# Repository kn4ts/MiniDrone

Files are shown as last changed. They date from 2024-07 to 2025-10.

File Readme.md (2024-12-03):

# Mini Drone
100g以下程度の小型ドローン製作を目指すプロジェクトです  

# 目次
1. [概要](#概要)
2. [マイコンのプログラムの基本構成](#マイコンのプログラムの基本構成)
3. [モータ駆動回路の基本構成](#モータ駆動回路の基本構成)
    - [モータの回転方向とプロペラについて](#モータの回転方向とプロペラについて)
    - [PWM出力・推力・電流の予備実験結果](#推力と電流とPWM値の測定実験)
4. [機体の作成](#機体の作成)
    - [概要](#部品の概要)
    - [機体の設計](#機体の設計)
    - [電気回路の構成](#電気回路の構成)
5. [ドローン制御系の基本構成](#ドローン制御系の基本構成)
6. [トラブルシュート](#トラブルシュート)
7. [参考ページ](#references)

# 概要
無線通信が可能なマイコンをフライトコントローラとして用い，地上局（PC）からのおおまかな指令をもとに飛行する小型ドローンを製作します．
特に制御実験に使用することを目指して，以下の要件を設定します．
+ 設定した制御周期を維持できること
+ 内界センサの計測値や計算した制御入力を逐次的に外部に出力できること
+ オリジナルの制御則やフィルタなどを容易に試せること

これらを実現するために，次のようなコードの流れを考えます．
（ここではマイコンとして`Arduino nano 33 BLE`（[https://ssci.to/7667](https://ssci.to/7667)）を使用することを想定していますが，相当の機能を持つマイコンであれば同様に構成可能と思います）

```mermaid
sequenceDiagram # シーケンス図の定義
    autonumber # 信号に番号をつける

    # 各要素の定義
    participant DebugDO as DO2<br>(デジタル出力ポート) # デバッグ用DOポート
    participant Sen as 測距センサ<br>(VL53L0X) # I2C接続
    participant Micon as マイコン
    participant PC as 地上局PC  # PC（地上局）

    Micon ->> Sen : I2C接続，周期設定
    PC ->> Micon: BLE接続

    loop BLE接続の持続 # ループの定義

        alt 制御用タイマーのフラグがオン # if文
            Note over Micon : IMU計測値から姿勢更新・取得
            Note over Micon : 現在の高度を取得
            # rect rgba(255, 0, 255, 0.2) # 色付け
            Note over Micon : 制御則の計算
            # end
            Note over Micon : PWM出力値更新 => FETへ

            Micon -->> DebugDO : DOポートをトグル（デバッグ用）
            Note over DebugDO : オシロスコープで100Hz出ているか確認
        end

        alt BLE通信用タイマーのフラグがオン
            Note over Micon : 現在の各内部変数からメッセージ作成
            # rect rgba(255, 0, 255, 0.2) # 色付け
            Micon ->> PC : BLE通信，メッセージ送信
            opt データロガー継続
                Note over PC : ファイルへ書き出し
            end
            # end
            Micon -->> PC : シリアル通信（デバッグ用）
        end

        alt 測距センサ用タイマーのフラグがオン
            Micon ->>+ Sen : I2C通信，測定値を要求
            Note over Sen : 注意：未準備だとブロック
            Sen ->>- Micon : I2C通信，測定値を返す
        end

        opt BLE通信による指令送信
            PC ->> Micon : BLE通信，指令送信
            Note over Micon : 指令解釈・モード変更
        end
    end

```
前述のタスクを達成しつつ制御周期を一定に維持するために，3つのタイマーを用いる構成としています．  

まず1つ目は制御則の動作周期をはかるタイマー`tmCon`で，ドローン制御で必要とされている100Hzに設定しています．こちらはデジタル出力ピンにパルス出力をさせてオシロスコープで100Hzが実現できることを確認しました．

2つ目はBLE通信（地上局への送信）のタイミングをはかるタイマー`tmBLE`で，これは`Arduino nano 33 BLE`マイコンで試したところ10Hz程度が安定する最高の速度でしたので10Hz程度で使用しています．（もちろん理想は制御周期と同じ100Hzでの通信ですが...）  

3つ目は機体高度を計測する測距センサから値を読みだす周期をはかるタイマー`tmToF`です．
使用するセンサ（VL53L0Xユニット，I2C接続）の仕様上，計測値の精度を高めるために数十ms必要で，また計測値が準備できていないと読み出し指令がブロックされる（※）とのことなので，少し長めに約33Hz(=30ms)の周期で読み込む時間管理をしています．
（こちらも制御周期と同じ100Hzで読むことが理想なのですが）

※【将来の課題】VL53L0XのGPIO1ピンはセンサが新しいデータを準備したときにトリガーされるそうなので，このピンをデジタルピンで監視しておけば回避できそうです．

またマイコンへの地上局からの指令もBLE通信を使用することにしていますが，こちらは頻繁な通信をしないという前提で，とりあえず時間管理なしで運用しています．今後，地上局も含めた閉ループを高速周期で構成する必要がでてくれば，そのためのタイマーを実装する必要がありそうです．

## 使用するライブラリ
+ `ArduinoBLE.h` ... BLE(Bluetooth Low Energy)を使用するためのライブラリ．
+ `Arduino_LSM9DS1.h` ... 9軸IMUのライブラリ．
+ `VL53L0X.h` ... ToF(Time of Flight)測距センサのライブラリ．

## 環境構築
1. Arduino IDE をインストール
2. Arduino IDE のボードマネージャから上記ライブラリをインストール  
参考：https://qiita.com/konikoni428/items/f4c7154ccf1eafd331c9

上記に加えて，BLE通信の動作確認のためにターミナルが使えると便利です．たとえばアプリの`LightBlue`など．

# マイコンのプログラムの基本構成
フライトコントローラの機能ごとにソースコードを分けて，メイン（`miniDrone.ino`）から呼び出して使用する構造にします．
これにより，機能の追加実装やテスト，複数人での開発が容易になることが期待できます．
```mermaid
graph TD
    classDef h fill:transparent, stroke:#9370DB
    classDef cpp fill:transparent
    classDef ino fill:transparent

    %% style some-group fill:transparent,stroke:#9370DB
    subgraph BLE [BLE機能のユニット]
        subgraph hBT [BLE.h]
            conBT[定数の定義]
            ~~~ proBT[関数のプロトタイプ宣言]
        end
        subgraph cppBT [BLE.cpp]
            valBT[変数の定義]
            ~~~ funBT[関数の中身の実装]
        end
        hBT --インクルード--> cppBT
        %%funBT --予め定義--> proBT
    end
    subgraph ControlTimer [Timer機能のユニット]
        subgraph hCT [ControlTimer.h]
            conCT[定数の定義]
            ~~~ proCT[関数のプロトタイプ宣言]
        end
        subgraph cppCT [ControlTimer.cpp]
            valCT[変数の定義]
            ~~~ funCT[関数の中身の実装]
        end
        hCT --インクルード--> cppCT
    end
    subgraph UnitX [・・・機能のユニット]
        subgraph hX [xxx.h]
            conX[定数の定義]
            ~~~ proX[関数のプロトタイプ宣言]
        end
        subgraph cppX [xxx.cpp]
            valX[変数の定義]
            ~~~ funX[関数の中身の実装]
        end
        hX --インクルード--> cppX
    end
    subgraph miniDrone[miniDrone.ino]
        inc1["#include "必要な機能1""]
        inc2["#include "必要な機能2""]
        incx["#include "必要な機能xxx""]

        subgraph Global[グローバル変数・関数]
            global[グローバル変数の定義]
            ~~~ globalfun[関数の定義]
        end

        subgraph loop[loop関数]
            callfunX[関数の使用]
        end
        
        setup[setup関数]

        inc1 -.- inc2
        inc2 -.- incx
        incx -.-> setup

        setup --> loop
        %%loop --ループ--> loop

        Global --> loop
        funX -.-関数の呼び出し-.-> callfunX
        %%funX -.-関数の呼び出し-.-> setup

        hBT --インクルード--> inc1
        hCT --インクルード--> inc2
        hX --インクルード--> incx
    end
```

最終的にはオリジナルの制御則やフィルタのコードは`Control.cpp`と`Control.h`のようなファイルにまとめるようにして，同じようにメインコードから呼び出して使用するような運用を考えています．
これにより設計者が極力メインコードを触ることなく制御則やフィルタを試せるようにしたいです．

# モータ駆動回路の基本構成
今回は設計を簡単にするために駆動系としてブラシ付きDCモータを使用することにします．
基本となるモータ1つ分の駆動回路を以下に示します．
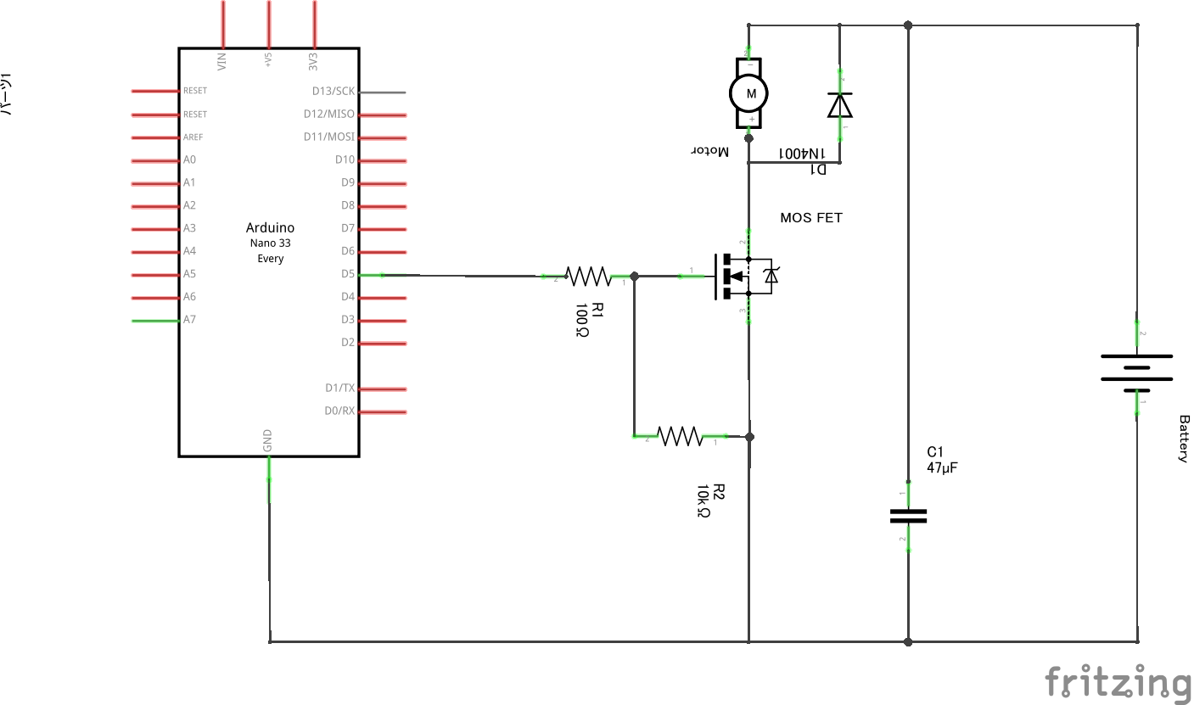
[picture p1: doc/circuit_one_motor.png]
回路図


ここではバッテリーからモータの駆動電流をとることとし，N-ch MOS FETを使って，駆動回路に流れる電流をマイコンのデジタル出力ピンから間接的に操作します．

また図では省略していますが，マイコンの電源はUSBケーブルから供給することを想定しています．
電源が異なるのでグラウンド（`GND`）の共通化を忘れないように注意してください．

この回路に使用している参考部品は以下の通りです．

**表1. モータ駆動回路の構成部品**
| 記号 | 名称 | 用途 | 型番  | 主な選定理由 |
| ----- | --- | -----| --- | ---|
| Motor | ブラシ付きDCモータ  | ロータ  | [8520モータ](https://www.amazon.co.jp/s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) | 100gクラスのドローン`Tello`の予備部品が流通しているため |
| MOS FET | N-ch 電界効果トランジスタ | 駆動回路のスイッチング | [2SK4017](https://www.google.com/search?client=firefox-b-d&q=2SK4017)など．部品のピン配置は[こちら](https://akizukidenshi.com/goodsaffix/2SK4017.pdf)を参照のこと． | 連続2A以上流せて，オン抵抗が低いFETを選定  |
| D1 | ダイオード | フライバックダイオード（逆起電力対策） | [SB240LES](https://akizukidenshi.com/catalog/g/g116419/)など | 駆動電圧より十分高い耐圧で，かつ連続2A以上流せるものを選定 |
| C1 | キャパシタ | バイパスコンデンサ（パスコン）| [積層セラミックコンデンサー 47μF16V](https://akizukidenshi.com/catalog/g/g104917/)など | 数十μFの容量があること |
| R1 | 抵抗器 | 電流調整用 | [1/4Wカーボン抵抗100Ω](https://www.marutsu.co.jp/pc/i/107016/)など | - |
| R2 | 抵抗器 | プルダウン抵抗？  | [1/4Wカーボン抵抗10kΩ](https://www.marutsu.co.jp/pc/i/107028/)など | - |
| Battery | 1S LiPoバッテリー  | モータの駆動電源  | [BETAFPV BT2.0 300mAh 1S 30Cバッテリー](https://amzn.asia/d/6Hk7pkt)など | 軽量かつ取扱いが容易で，連続8A以上の放電能力があること |

なお，こちらの回路を使用してモータを駆動させるテストコードは[こちら](https://github.com/kn4ts/MiniDrone/releases/tag/actuator-test)からアクセスできます．
使い方は，BLE通信で接続後，String型で"1"~"9"を送信すると`20`～`255`までのPWM値をD5～D8ピンから出力します（"0"を送ると停止）．モータが回転するので注意してください．

## モータの回転方向とプロペラについて
なおプロペラは`Tello`のスペアパーツとして流通している[こちら](https://amzn.asia/d/75Xps07)やその代替品を使用します．
8520モータの軸に差し込むだけで使用可能です．  
なお8520モータには2種類あり，線の色で見分けられるようです．
線の色と回転方向は以下の表の通りです．

**表2. モータの回転方向**
|モータの線の色|回転方向|
| --- | --- |
|白(-側)と黒(+側)|CW（時計まわり）|
|青(-側)と黒(+側)|CCW（反時計回り）|

そしてこのモータの回転方向に合ったプロペラを取り付けます．
また4つのロータで飛行するクワッドロータドローンでは，対角に同じ回転方向のロータを配置する必要がありますので注意してください．

## 推力と電流とPWM値の測定実験
前述の回路構成をもとに4つのロータを駆動する予備的な実験を行いました．
実験の様子を以下に示します．
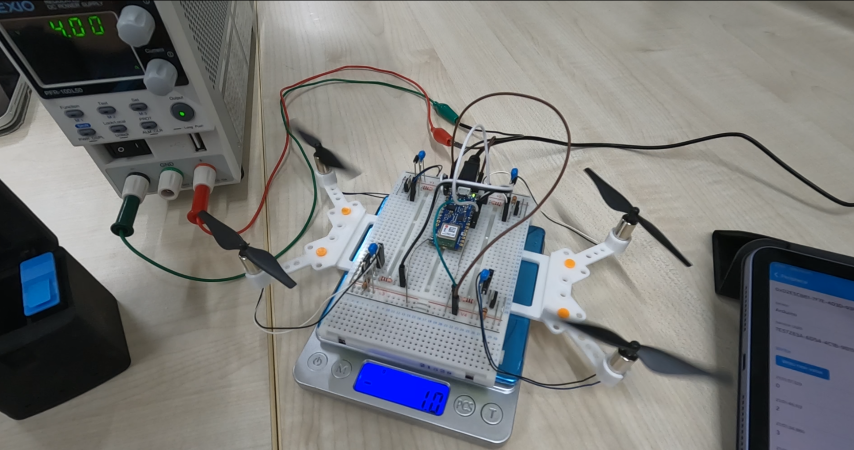
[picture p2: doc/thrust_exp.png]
予備実験の装置構成


ここではモータ駆動用の電源として安定化電源を使用（4.00Vで最大電流値10Aに設定）し，マイコン電源はUSBから供給しました．
またマイコン含む回路部分全体を重量計の上に置き，いくつかのPWM値で4つのロータを同時に駆動した際の重量計の値の減少量とそのときの電源装置の出力電流をメモしました．

その結果を1つの図にプロットしたものを以下に示します．
なお，これらの計測値は定常状態のもの（目視で値が落ち着いたところで読み取ったもの）であるため，結果は参考値です．

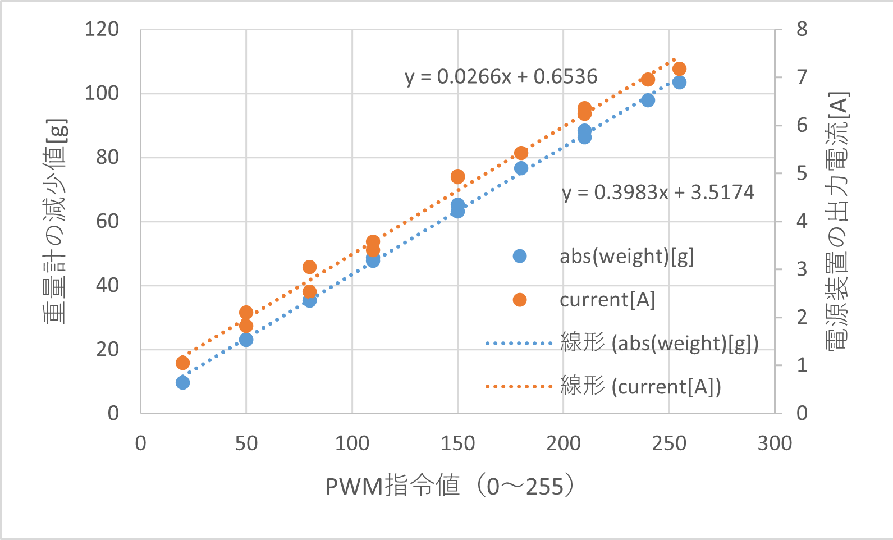
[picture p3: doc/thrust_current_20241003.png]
推力-電流-PWM指令値の測定結果


この結果から，マイコンに指令するPWM値に対して推力（正確には重量計表示の減少量[g]），電流[A]がいずれもほぼ線形に推移していることが読み取れます．

また推力と電流値を比較することで，機体重量に対する使用バッテリーに要求される放電能力や，飛行可能時間を概算できます．

# 機体の作成
## 部品の概要
+ Arduino nano 33 BLE ... BLEモジュールとIMUが搭載されたマイコン（[https://ssci.to/7667](https://ssci.to/7667)）
+ VL53L0X Time-of-Flight 距離センサモジュール ... ToF測距センサ（[https://ssci.to/2894](https://ssci.to/2894)）
+ 電圧レギュレータ ... マイコン電源用．5V出力ステップアップ／ステップダウン電圧レギュレータ（[https://ssci.to/1168](https://ssci.to/1168)）

## 機体の設計
機体のフレームは[電気回路の設計・配置](#電気回路の構成)と合わせて，サイズや構造を考えて設計します．
具体的には，モータや基板の固定方法やセンサの配置，バッテリーの搭載位置などを検討する必要があります．
また機体の中心からみて重量の偏りがない方が，制御設計や飛行特性が扱いやすいものになりそうです．

[（参考）機体フレームのSTLデータ](./hardware/Frame/frame_A_ver3.stl)  
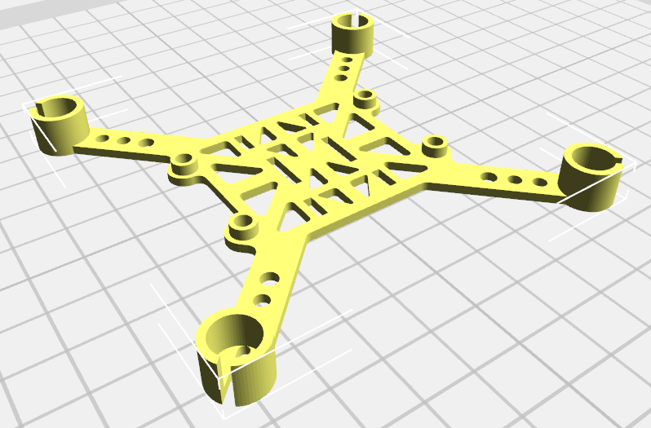
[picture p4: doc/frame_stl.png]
機体フレームの設計


## 電気回路の構成
以下に駆動系・測距センサ・電圧レギュレータを含めた全体の回路図を示します．

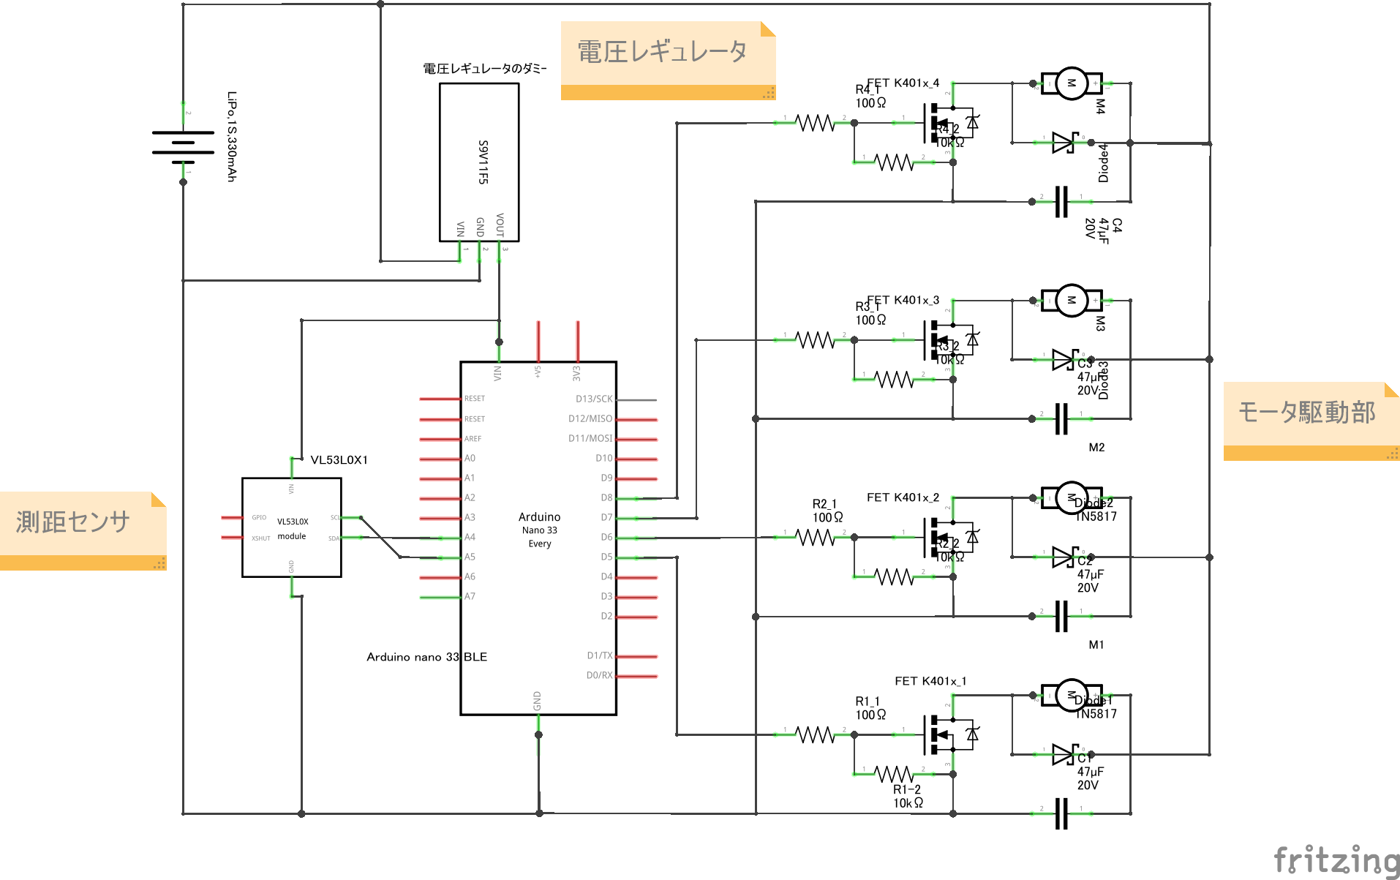
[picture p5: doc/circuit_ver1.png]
ドローン全体の回路図


ドローンではマイコン電源もバッテリーからとる必要があるので，電圧レギュレータを挟んで昇降圧したラインをマイコンの`VIN`ピンに接続しています．
また測距センサの駆動電源も，同じくレギュレータからとるようにしています．

こちらの回路図をもとに実体配線図を作成し，基板上に部品を配置してください．
回路や実体配線図の製作については，[fritzing](https://fritzing.org/)や[PasS](http://uaubn.g2.xrea.com/pass/)，Eagleなどを使用すると便利です．

[（参考）回路図データ](./circuit/fritzing/circuit_ver1.fzz)  
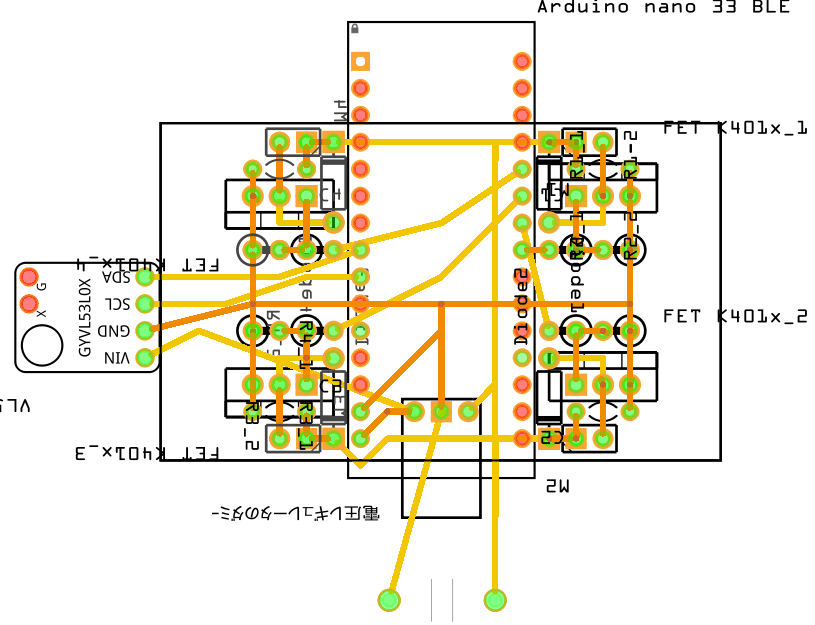
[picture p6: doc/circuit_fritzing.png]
実体配線図の一例


# ドローン制御系の基本構成
ドローンの姿勢（ロール，ピッチ．ヨー）角と高度を制御するための制御系のブロック線図の概要を以下に示します．

ブロック線図

ここでは，制御対象（プラント）への入力信号（制御入力）を各ロータの駆動回路（[こちらです](#モータ駆動回路の基本構成)）をスイッチングするPWM信号値（デューティ比）とし，出力信号（制御量）を機体の姿勢角および高度として解釈します．

以下では，このドローンの制御系を構成するために必要な3つの要素についてそれぞれ説明します．

## ①姿勢・高度推定器
制御量である姿勢角と高度はそれぞれ9軸IMUと測距センサにより計測します．
ただしこれらの計測値はノイズやバイアス成分を含んでいると考えられるため，計測された信号をもとに姿勢や高度の推定器を構成します．
この推定器としては，例えば相補フィルタやカルマンフィルタが使用されることが多いようです．

## ②制御器
そして（推定器で求められた）姿勢角と高度に対してそれぞれ制御器を構成します．
制御器は制御量と参照値（目標値）をもとに，次にどのような制御入力を制御対象に加えるかを決定する機構です．

ここでは姿勢角制御器は機体の3つの回転軸（ロール，ピッチ，ヨー）まわりに要求されるトルクに相当する信号値を計算し，高度制御器は4つのロータに要求される総推力に相当する信号値を計算する，と解釈しています．
上の図では，これらの3つのトルクと1つの総推力をまとめて要求制御力と表現しています．
要求制御力をベクトルで表現するとトルク3つと総推力1つで合計4次元を持ちます．

## ③分配器（ミキシング則）
要求制御力はそのままでは制御入力として使用できないため，要求制御力をもとに各ロータを駆動するPWM値を計算する機構が必要で，これを上図では分配器（ミキシング則）と表現しています．
分配器を設計する上では，姿勢角の軸のとり方とプロペラの配置・回転方向を考慮する必要があります．

以上の推定器・制御器・分配器を適切に設計してドローンの制御系を構成します．
なお，これら3つをまとめて制御器と呼ぶ場合もあります．

# ドローン制御則の実装
`miniDrone.ino`の制御周期のタイミングにおける具体的な計算の流れを以下のシーケンス図で説明します．

```mermaid
sequenceDiagram # シーケンス図の定義
    autonumber # 信号に番号をつける

    # 各要素の定義
    participant Main as 制御周期における処理 <br>（miniDrone.inoの中）
    participant Class as 

    opt IMU計測値の更新・取得
        Note right of Class: IntegratedIMU.cpp
        Main ->> Class : updateIMUAttitudeVal() <br> （姿勢値の更新指令）
        Class ->> Main : ATTITUDE = getIMUAttitude_wo_b() <br> （バイアス値抜きの姿勢を取得）
        Class ->> Main : ANG_VEL = getIMUAngularVelocity_wo_b() <br> （バイアス値抜きの姿勢角速度を取得）
        Class ->> Main : MAG = getIMUMag() <br> （地磁気センサの値を取得） 
    end

    opt 高度計測値の取得
        Note right of Class: SencorI2C.cpp
        Class ->> Main : ALTITUDE = getAltitudeVal_wo_b() <br> （バイアス値抜きの高度を取得）
    end

    opt 姿勢・高度制御則の計算例
        Note right of Class: Control.cpp <br> （構成例）
        Main ->> Class : set{Roll,Pitch}Reference( REF ) <br> （姿勢角の参照値をセット）
        opt 制御器の計算 
        Main -> Class : PWMs = controller_demo( ATTITUDE, ALTITUDE ) <br> （フィードバック信号である姿勢，高度を引数として渡す）
            Note over Class : フィルタ計算
            Note over Class : 制御則計算
            Note over Class : 分配器計算
        Class ->> Main : PWMs = controller_demo( ATTITUDE, ALTITUDE ) <br> （計算結果のPWM信号値の配列の先頭ポインタを返す）
        end
    end

    alt Arm状態なら
        Note right of Class: Actuator.cpp
        Main ->> Class : REAL_PWMs = driveActuator( PWMs ) <br> （PWM指令値を使ってロータを駆動，<br> 飽和後のPWMsを返す）
    else Disarm状態なら
        Main ->> Class : REAL_PWMs = driveActuator( PWM_ZEROs ) <br> （0の入力を使ってロータを駆動（つまり停止），<br> 飽和後のPWMsを返す）
    end

```
---
---

# トラブルシュート
## デバイスマネージャで COM xx が認識されない
下記を試す．  
+ PCの再起動
+ Arduino IDE のバージョン更新確認
+ Arduino IDE でボード情報の更新
+ マイコンのリセットボタンを押しながら接続

コードが間違っていてマイコン側のUSB Serialが機能しなくなっている可能性がある．その場合は以下を試す．
+ マイコンのリセットボタンをダブルタップ -> 違うCOMポートとして認識 -> 認識したCOMポートで正しいコードを書き込み

## References
### フォルダ構成は下記を参考にした  
+ https://qiita.com/somehiro/items/6a6d954be159b6a5fccd  
+ https://zenn.dev/skou/articles/7a49ca2f9f0fcc

### 駆動系の電気回路は下記を参考にした
+ https://www.remma.net/?p=1341

### COMが認識されなくなる問題のトラブルシュート  
+ https://detail.chiebukuro.yahoo.co.jp/qa/question_detail/q11263532971

### Mermaidの参考ページ
+ https://qiita.com/run1000dori/items/90f91687cfe7ece50020

### VSCodeでDrawioを使って作図する拡張機能について
+ https://otepipi.hatenablog.com/entry/2020/05/25/192844

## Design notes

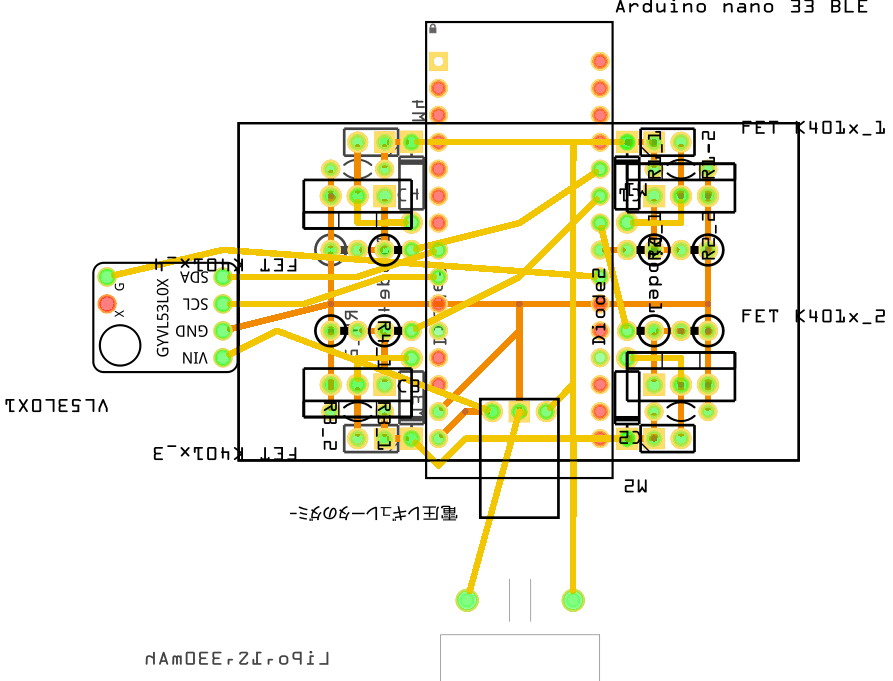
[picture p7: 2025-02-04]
doc/circuit_ver2_fritzing.png

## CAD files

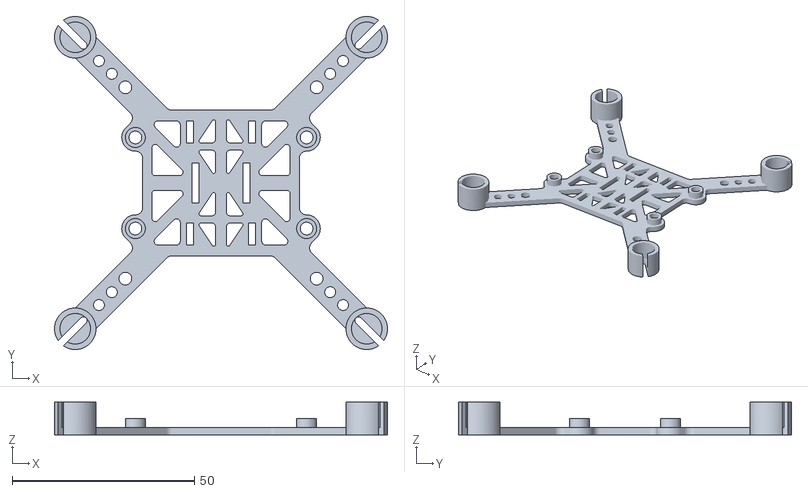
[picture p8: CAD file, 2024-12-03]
hardware/Frame/frame_A_ver3.1.stl
91.4 x 91.4 x 9.00

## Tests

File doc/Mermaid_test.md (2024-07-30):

# Mermaid をMarkdownで使うテスト
```mermaid
block-beta

%% 信号用に枠線なしのブロックをクラスとして定義
classDef signal stroke-width:0px
%% 信号分岐用に黒塗りのブロックをクラスとして定義
classDef split fill:black

columns 9
ref["参照入力"] plus(("+")) space cont["制御器"] space plant["プラント"] split1((" ")) space out["出力"]
space:9
space lb["└"] space:4 rb["┘"]

class ref,out,lb,rb signal
class split1 split

ref --> plus
plus --> cont
cont --> plant
plant --> split1
lb --> plus
split1 --> rb
split1 --> out
rb --> lb

```
TEST

```mermaid
flowchart LR
    Reference --> plus1(("+"))
    plus1 --- Controller
    Controller --- Plant
    Plant --- split1((" "))
    split1 --> Output

    %%Output --- Minus1["-1"]

    split1 --- Minus1
    Minus1 --> plus1
    %%<!-- Null2 --> plus1 -->

    classDef signal stroke:none
    classDef split fill:black,stroke:white
    classDef plusminus stroke:white

    class Reference,Output signal
    class split1 split
    class plus1 plusminus
```

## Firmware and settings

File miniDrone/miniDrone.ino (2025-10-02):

/* ==================================================================
  メインのソースコード
================================================================== */
#include "src/inc/miniDrone.h" // 全体のヘッダファイル


/* ==================================================================
  セットアップ関数
================================================================== */
void setup() {
  /* 出力ピンの設定 */
  pinMode( LED_BUILTIN, OUTPUT ); // 内臓LEDの設定（デバッグ用）
  pinMode( STATE_DO, OUTPUT );  // 制御周期確認用DOポートの設定（デバッグ用）
  setupPWMpin(); // PWM出力ピンの初期化

  /* シリアル通信の初期設定 */
  openSerial();

  /* BLEの初期設定 */
  if( !setupBLE() ){
    // 失敗したらエラー表示で止まる
    while(1){
      Serial.println("BLE setup error!");
      delay(2000);
    };
  }

  /* タイマーの初期設定 */
  setupTimer();

  /* 内臓IMUの初期化 */
  if( !initIMU() ){
    // 失敗したらエラー表示で止まる
    while(1){
      Serial.println("IMU setup error!");
      digitalWrite( LED_BUILTIN, HIGH );
      delay(500);
      digitalWrite( LED_BUILTIN, LOW );
      delay(500);
    };
  }

  /* I2Cセンサの初期化 */
  if( !initSensorI2C() ){
    // 失敗したらエラー表示
    Serial.println("I2C sensor setup error!");
    delay(2000);
  }

}

/* ==================================================================
  メインループ関数
================================================================== */
void loop() {
  /* BLE接続を試行する */
  listenBLE(); // セントラル機器との接続確認
  pollBLE(); // BLEスタックの更新

  /* BLE接続されていたら実行される部分 */
  if ( isConnectedToPeripheral() ){ // セントラルがペリフェラルに接続されているかの確認
    /* BLEセントラルに接続されている間ループ */
    while ( centralStillConnected() ){

      // BLE通信の指令の受信・解釈
      mode = modeDetectionBLE();

      // モードに応じた動作（一度きり実行）
      switch (mode){
        // 制御開始準備
        case MODE_CONTROL_STANDBY:  // mode が CONTROL_STANDBY なら
          setAltitudeReference(300); mode = MODE_CONTROL; break; // 高度目標値をセット・モードをCONTROLへ移行
        
        // センサキャリブレーション
        case MODE_CALIBRATE_SENSORS: // センサキャリブレーション
          calibrateSensors();
          //calibrateGyroBias(); // ジャイロセンサのバイアスを再取得
          mode = MODE_NORMAL; break;

        // 姿勢角キャリブレーション
        case MODE_CALIBRATE_ATTITUDE: // 姿勢角キャリブレーション
          calibrateAttitude();
          mode = MODE_NORMAL; break;

        // Arm
        case MODE_ARM:
          armDrone();
          //arm = true;
          initializeController(); // 制御器をリセット
          mode = MODE_NORMAL; break;

        /* 目標値セット */
        //case MODE_FORWARD:
        //  cnt_pit = -cnt_MAX; mode = MODE_NORMAL; break; // カウンタを-最大値へ
        //case MODE_BACKWARD:
        //  cnt_pit =  cnt_MAX; mode = MODE_NORMAL; break; // カウンタを最大値へ
        //case MODE_LEFT:
        //  cnt_rol = -cnt_MAX; mode = MODE_NORMAL; break; // カウンタを最大値へ
        //case MODE_RIGHT:
        //  cnt_rol =  cnt_MAX; mode = MODE_NORMAL; break; // カウンタを最大値へ

        /* 停止モード */
        case MODE_STOP: 
          disarmDrone();
          break;

        /* 上記以外の場合はスルー */
        default:
          //initializeController(); // 制御器をリセット
          //uc_pointer = setUc( 0, 0, 0, 0 ); // 制御器出力をすべて0に
          break;
      }


      /* -------------------------------
         制御周期タイマー処理のはじまり
      ------------------------------- */
      if ( getTmConFlag() ){
        setTmConFlag(false); // タイマー割込みフラグをおろす

        /*
          指令値カウンタの確認・処理
        */ 
        updateRollPitchReference( cnt_rol, cnt_pit ); // ロール・ピッチ角指令値の更新

        // IMUセンサ値を用いた姿勢角の更新
        //updateIMUAttitudeVal();
        updateIMUAttitudeVal_ver2();

        // IMUで計算した値を取得
        att = getIMUAttitude_wo_b(); // 姿勢を取得
        anv = getIMUAngularVelocity_wo_b(); // 角速度を取得
        // 地磁気計測値を取得
        // mag = getIMUMag(); 

        /* ToFセンサから届いている最新の高度を取得 */
        if ( getToFFlag() ){
          setToFFlag(false); // ToFセンサフラグをおろす
          // 注意：測定値が準備できていないとブロックする
          //updateAltitudeVal();
          updateAltitudeVal();
          alt = getFilteredAltitudeVal_wo_b();
        }

        /*
          高度・姿勢の異常検知
        */
        if( abs(att[0]) > 90 ){ mode = MODE_STOP; }; // ロール角が異常ならモードを0に
        if( abs(att[1]) > 90 ){ mode = MODE_STOP; }; // ピッチ角が異常ならモードを0に

        /*
          モードに応じた動作（継続実行）
          モードの一つとして制御則を実装する
        */
        switch (mode){
          /* 停止モード */
          case MODE_STOP: // mode が 0 ならロータ停止
            disarmDrone();  // ドローンをディスアーム
            uc_pointer = setUc( 0, 0, 0, 0 ); break;

          /* 全モータの動作テストモード */
          case MODE_TEST_ALL_MOTORS:
            uc_pointer = setUc( 20, 20, 20, 20 ); break; // 全モータをPWM値20で回す指令
          
          /* 制御モード */
          case MODE_CONTROL: // mode が 10 なら制御実行
            // 制御モード時の異常検知
            if( alt > 2000 ){ mode = MODE_STOP; };       // 高度計測値が異常ならモードを0に

            // 制御則の計算
            uc_pointer = controller_demo( att, alt ); // 制御則関数
            uc[0] = uc_pointer[0]; // 制御器出力をucにセット
            uc[1] = uc_pointer[1];
            uc[2] = uc_pointer[2];
            uc[3] = uc_pointer[3];
            break;
          
          /* ジンバル制御モード（ロール・ピッチ） */
          case MODE_GIMBAL_ROLL_PITCH: // 2DoFジンバル（ロールピッチ軸）の姿勢制御モード
            //uc_pointer = gimbalControl_demo( att, alt ); // ジンバル使用時の制御則
            uc_pointer = gimbalControl_demo( att, anv, alt ); // ジンバル使用時の制御則
            uc[0] = uc_pointer[0]; // 制御器出力をucにセット
            uc[1] = uc_pointer[1];
            uc[2] = uc_pointer[2];
            uc[3] = uc_pointer[3];
            break;
          
          /* ジンバル制御モード（ロールのみ） */
          case MODE_GIMBAL_ROLL: // 1DoFジンバル（ロール軸のみ）の姿勢制御モード
            //uc_pointer = gimbalControl_demo( att, alt ); // ジンバル使用時の制御則
            uc_pointer = gimbalControl_1dof_demo( att, anv, alt ); // ジンバル使用時の制御則
            uc[0] = uc_pointer[0]; // 制御器出力をucにセット
            uc[1] = uc_pointer[1];
            uc[2] = uc_pointer[2];
            uc[3] = uc_pointer[3];
            break;

          /* アイドリングモード */
          case MODE_IDLE:
            uc_pointer = idle_thrust( ); // アイドル推力をセット
            uc[0] = uc_pointer[0]; // アイドリング入力をucにセット
            uc[1] = uc_pointer[1];
            uc[2] = uc_pointer[2];
            uc[3] = uc_pointer[3];
            break;

          /* ロール角動作の確認モード */
          case MODE_TEST_ROLL:
            uc_pointer = test_roll( att );
            uc[0] = uc_pointer[0]; // 入力をucにセット
            uc[1] = uc_pointer[1];
            uc[2] = uc_pointer[2];
            uc[3] = uc_pointer[3];
            break;

          /* ピッチ角動作の確認モード */
          case MODE_TEST_PITCH:
            uc_pointer = test_pitch( att );
            uc[0] = uc_pointer[0]; // 入力をucにセット
            uc[1] = uc_pointer[1];
            uc[2] = uc_pointer[2];
            uc[3] = uc_pointer[3];
            break;
          
          /* 上記以外のモード時 */
          default: // mode のデフォルト設定
            uc_pointer = setUc( 0, 0, 0, 0 ); break; // 全入力を0に
        }

        // アクチュエータを駆動する
        if( isArmed() == true ){
          up_pointer = driveActuator( uc_pointer ); // 制御器出力でアクチュエータを駆動
        }else{
          up_pointer = driveActuator( &u0[0] ); // 入力0で駆動
        }

        // デバッグ用DOポートをトグル -> 100Hz出ているか確認用
        toggleDO();
      }
      /* -------------------------------
         制御周期タイマー処理ここまで
      ------------------------------- */

      /* -------------------------------
         BLE通信用タイマー処理のはじまり
      ------------------------------- */
      if ( getTmBleFlag() ){ 
        setTmBleFlag(false); // BLE割り込みフラグをおろす

        // マイコンの中の時刻を取得
        unsigned long currentTime = millis();

        // 制御器内部の情報を取得
        float* control_force = getControlForceReq(); // 要求制御力を取得
        //float alt_fil = getFilteredDistanceVal_wo_b(); // フィルタ処理後の高度を取得
        float alt_wo_b = getAltitudeVal_wo_b(); // バイアス処理後の高度を取得
        float rol_fil = getRollFiltered(); // フィルタ処理後のロール角を取得
        float pit_fil = getPitchFiltered(); // フィルタ処理後のピッチ角を取得
        float yaw_fil = getYawFiltered(); // フィルタ処理後のヨー角を取得
        float ref_alt = getAltitudeReference(); // 高度指令値を取得
        float ref_rol = getRollReference(); // ロール角指令値を取得
        float ref_pit = getPitchReference(); // ピッチ角指令値を取得

        // BLE通信の送信メッセージを作成
        setMsgSendBLE( currentTime, att, anv, alt_wo_b, control_force,
                   alt, rol_fil, pit_fil, yaw_fil,
                   ref_alt, ref_rol, ref_pit ); // 送信メッセージ作成
        sendMessageBLE(msgSendBLE); // メッセージ送信

        // BLE通信の受信メッセージを確認
        char msgRecvBLE = getWrittenMessageHead(); // 1文字のメッセージを取得

        // シリアル通信でメッセージ送信（デバッグ用）
        //Serial.print(msgRecvBLE); Serial.print(", "); Serial.print(getToFFlag()); Serial.print(", "); Serial.println(alt);
      }
      /* -------------------------------
         BLE通信用タイマー処理ここまで
      ------------------------------- */
    }
  }

  mode = MODE_STOP; // モードをリセット
  disarmDrone(); // ドローンをディスアーム
  uc_pointer = setUc( 0, 0, 0, 0 ); // 入力を初期化
  up_pointer = driveActuator( &u0[0] ); // モータ止める

  printNoCentral( getBLEAddress() ); // セントラル機器がないことをシリアルで表示
  delay(4000);
}

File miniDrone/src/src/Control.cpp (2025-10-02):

/*
    制御系に関するソースファイル
     姿勢制御，高度制御など
     ・関連ライブラリのインクルード
     ・関連変数の宣言
     ・関連関数の宣言
*/
#include "../inc/Control.h"

// 目標値
static float ref_alt = 20;  // 高度目標値[mm]の初期値
static float ref_rol = 0;   // ロール目標値[degree]の初期値
static float ref_pit = 0;   // ピッチ目標値[degree]の初期値
static float ref_yaw = 0;   // ヨー目標値[degree]の初期値

/* 制御器ゲイン */
// 高度ゲイン
static AltGain altK = { 0.2, 0.05, 0.03 }; // 高度制御器ゲインの構造体（P, I, D の順）
// ロール角度ゲイン
//static RollGain rolK = { 2.0, 0.0, 0.5 }; // ロール角度ゲインの構造体（P, I, D の順）
//static RollGain rolK = { 2.0, 0.0, 1.0 }; // ロール角度ゲインの構造体（P, I, D の順）
//static RollGain rolK = { 0.5, 0.0, 0.0 }; // ロール角度ゲインの構造体（P, I, D の順）
//static RollGain rolK = { 0.5, 0.0, 1.0 }; // ロール角度ゲインの構造体（P, I, D の順）
//static RollGain rolK = { 1.5, 0.0, 1.5 }; // ロール角度ゲインの構造体（P, I, D の順）
static RollGain rolK = { 1.0, 0.0, 1.0 }; // ロール角度ゲインの構造体（P, I, D の順）
// ピッチ角度ゲイン
static PitchGain pitK = { 0.5, 0.0, 1.0 }; // ピッチ角度ゲインの構造体（P, I, D の順）
//static PitchGain pitK = { 2.0, 0.0, 0.5 }; // ピッチ角度ゲインの構造体（P, I, D の順）

// ロール・ピッチ方向PID制御器出力の最小・最大値
static float controller_output_max = 10.0 ; // 試行錯誤

/* 制御器の内部変数 */
static AltVariable alt = { 0, 0, 0, 0, 0, 0 }; // 高度に関するもの
static RollVariable rol = { 0, 0, 0, 0, 0, 0}; // ロール角度に関するもの
static PitchVariable pit = { 0, 0, 0, 0, 0, 0}; // ピッチ角度に関するもの
static YawVariable yaw = { 0, 0, 0, 0, 0, 0}; // ヨー角度に関するもの

// 計測値のフィルタ処理用の変数
static LowpassFilterGain alpha = { 0.1, 0.15, 0.15, 0.15 }; // 高度，ロール，ピッチ，ヨーの順

// 要求制御力
static float cont_force[4] = { 0, 0, 0, 0} ; // 要求制御力をまとめる配列
// 制御器出力
static float uc[4] = { 0, 0, 0, 0}; // 制御器出力の配列
// バイアス入力
static float u_bias = 20; // ホバリングのためのバイアス入力成分，試行錯誤
// オフセット入力
static float u_offset[4] = {6,6,7,9}; // モータ個体差の補償のためのオフセット入力，試行錯誤
// アイドリング時の入力
static float u_idle = 10 ; // アイドリング時の入力

// 制御器実装用の変数
static unsigned long prevTime, currTime ; // 時刻の差分をとるための変数（ミリ秒）
static unsigned long prevTime_us, currTime_us ; // 時刻の差分をとるための変数（マイクロ秒）
static float deltaTime ; // 時刻の差分を格納する変数（秒）

// 飛行状態の把握に使う？内部変数
static int8_t status = 0 ; // ステータス

/* 関数定義 */
// 制御器の実装例
//   引数：フィードバックされる信号
//   返り値：PWM指令値の配列の先頭アドレス
float* controller_demo( float* y, float alti ){

    // 時間算出
    currTime = millis(); // 現在時刻の取得
    deltaTime = min( 0.001 * (currTime - prevTime), 0.02 ) ; // 前回からの差分時間[s]を計算，最大でも0.02[s]に制限
    prevTime = currTime; // 前回時刻を更新

    /* -------------------------------
        信号の更新
    ------------------------------- */ 
    // ロール角度情報
    rol.filt = lowpassFilterRoll_demo( rol.filt_prev, y[0] ) ; // ロール角計測値にローパスフィルタをかける
    //
    //rol.e = ref_rol -y[0] ; // 現在の誤差
    rol.e = ref_rol -rol.filt ; // 現在の誤差
    rol.ed = ( rol.e -rol.e_prev ) / deltaTime ; // 誤差を数値微分
    rol.ei += rol.e * deltaTime ; // 誤差の積分
    //
    rol.e_prev = rol.e ; // 1ステップ前のロール角誤差を更新
    rol.filt_prev = rol.filt ; // 1ステップ前のフィルタ処理後のロール角を更新

    // ピッチ角度情報
    pit.filt = lowpassFilterPitch_demo( pit.filt_prev, y[1] ) ; // ピッチ角計測値にローパスフィルタをかける
    //
    //pit.e = ref_pit -y[1] ; // 誤差
    pit.e = ref_pit -pit.filt ; // 誤差
    pit.ed = ( pit.e -pit.e_prev ) / deltaTime ; // 誤差の数値微分
    pit.ei += pit.e * deltaTime ; // 誤差の積分
    //
    pit.e_prev = pit.e ; // 1ステップ前のピッチ角誤差を更新
    pit.filt_prev = pit.filt ; // 1ステップ前のフィルタ処理後のピッチ角を更新

    // ヨー角度情報
    yaw.filt = lowpassFilterYaw_demo( yaw.filt_prev, y[2] ) ; // ヨー角計測値にローパスフィルタをかける
    //
    //pit.e = ref_pit -y[1] ; // 誤差
    yaw.e = ref_pit -y[2] ; // 誤差
    yaw.ed = ( yaw.e -yaw.e_prev ) / deltaTime ; // 誤差を数値微分
    yaw.ei += yaw.e * deltaTime ; // 誤差の積分
    //
    yaw.e_prev = yaw.e ; // 1ステップ前の誤差を更新
    yaw.filt_prev = yaw.filt;

    // 高度情報
    //alt.filt = lowpassFilterAltitude_demo( alt.filt_prev, distance ) ; // 高度計測値にローパスフィルタをかける
    alt.corr = compensationWithAttitude( alti, rol.filt, pit.filt );
    //
    alt.ed = ( -alt.corr +alt.corr_prev ) / deltaTime ; // 微分先行で計測値を数値微分
    alt.e = ref_alt -alt.corr ; // 現在の誤差
    alt.ei += alt.e * deltaTime ; // 誤差の積分
    //
    alt.corr_prev = alt.corr ; // 1ステップ前のフィルタ後高度を更新
    //
    // ステータス（飛行状況）の判定・更新
    if( status == 0 && alt.corr > 6 ){ status = 1; } // 離陸

    // 要求制御力の計算
    float tau_rol = rolK.p * rol.e + rolK.i * rol.ei + rolK.d * rol.ed ; // ロール方向
    float tau_pit = pitK.p * pit.e + pitK.i * pit.ei + pitK.d * pit.ed ; // ピッチ方向
    float tau_yaw = 0.0 ;
    float f_total = altK.p * alt.e + altK.i * alt.ei + altK.d * alt.ed ; // 高度方向

    // 制御器出力の飽和
    tau_rol = saturate_controller_rollpitch( tau_rol );
    tau_pit = saturate_controller_rollpitch( tau_pit );

    // ミキシング（分配）
    allocator_demo( tau_rol, tau_pit, tau_yaw, f_total );

    // 変数保存&更新
    cont_force[0] = tau_rol;
    cont_force[1] = tau_pit;
    cont_force[2] = tau_yaw;
    cont_force[3] = f_total;

    // 計算した制御入力（PWM値）の配列の先頭アドレスを返す
    return &uc[0];
}
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

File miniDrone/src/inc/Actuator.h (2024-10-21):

/*
    駆動系に関するヘッダファイル
     ・関連ライブラリのインクルード
     ・関数のプロトタイプ宣言
*/
#ifndef Actuator_h // 複数回読み込みを防ぐif def文
    #define Actuator_h

    #include<Arduino.h>

    /* ピン定義
        4   1
         \ /
          ↑ head
         / \
        3   2

        番号    |  1  |  2  |  3  |  4  |
        回転方向 | CCW | CW | CCW  | CW |
        ピン配置 | D5 | D6  | D7  | D8  |
    */
    #define PWM_1 D5
    #define PWM_2 D6
    #define PWM_3 D7
    #define PWM_4 D8

    // アクチュエータの調整パラメータ
    // #define MIN_PWM_CW 70 // CW方向回転のPWMの最小値
    // #define MIN_PWM_CCW 64    // CCW方向回転のPWMの最小値

    //#define MAX_PWM 200 // PWM の最大値（※注意※単一モータで過大なPWM値を使用するとFETが燃える？）→200くらいなら大丈夫そう
    #define MAX_PWM 180 // PWM の最大値（※注意※単一モータで過大なPWM値を使用するとFETが燃える？）→255でも大丈夫そう
    //#define MAX_PWM 200 // PWM の最大値（※注意※単一モータで過大なPWM値を使用するとFETが燃える？）→255でも大丈夫そう
    //#define MAX_PWM 255 // PWM の最大値（※注意※単一モータで過大なPWM値を使用するとFETが燃える？）→255でも大丈夫そう

    // 関数のプロトタイプ宣言
    void setupPWMpin();   // PWMピンの初期化関数

    int* driveActuator( float* uc );

    int saturatePWM(int ui);
    void set_PWM_4ch(int u1, int u2, int u3, int u4);   // 4chのPWM出力設定
    // uint16_t getAltitudeVal();  // 高度計測値のゲッタ関数

#endif  // if def文の終わり

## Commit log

2024-09-13 add test code for pwm output
2024-10-02 make actuator header
2024-10-02 update readme for actuator test
2024-10-03 fix code for Actuator test
    [Actuator.h, miniDrone.ino]
2024-10-03 fix readme with circuit diagram
2024-10-08 fix IMU code
2024-10-08 add calibration code for sensors
2024-10-08 add host code and demo data
    [exp_20241008_075955.csv]
2024-10-09 add pid control for altitude control
2024-10-15 add pid control for roll & pitch
2024-10-16 update ble send and pid gain
2024-10-20 implement lowpass filter for attitude
2024-10-25 implement key interruption
2024-10-25 compatible with no ToF sensor
2024-10-29 upload timer class
2024-11-01 fix ble msg code
    [miniDrone.ino]
2024-12-03 update readme with circuit and frame
    [circuit_ver1.fzz, frame_A_ver3.1.stl]
2024-12-04 stop using timer fo ToF sensor by activating GPIO1 pin on ToF sensor
2025-02-04 add circuit ver.2
    [circuit_ver2.fzz]
2025-09-18 fix anomaly detection on gimbal mode
    [miniDrone.h, miniDrone.ino]
2025-09-26 update IMU function for REV2
